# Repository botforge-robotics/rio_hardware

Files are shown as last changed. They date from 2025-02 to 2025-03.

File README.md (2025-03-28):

<p align="center">
    
    
    
    
    
    
    
    
    
</p>

<p align="center">
    <h1 align="center">RIO Hardware</h1>
</p>
<p align="center">
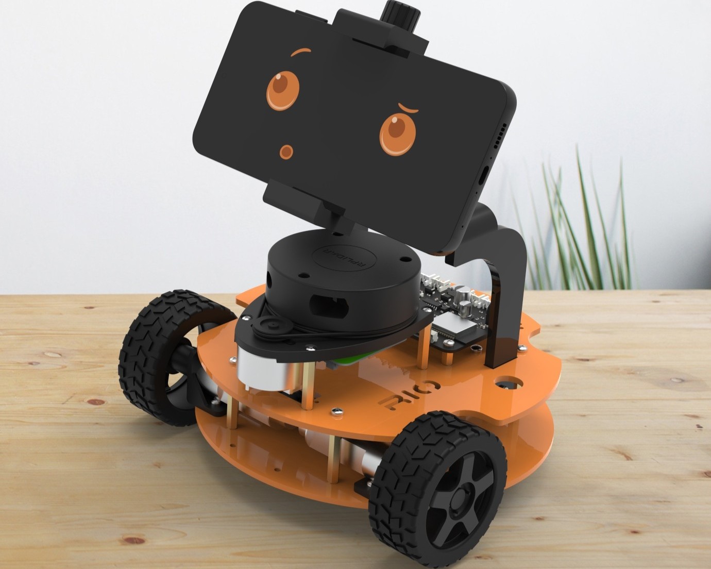
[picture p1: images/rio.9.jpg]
RIO Robot
    
</p>

## Table of Contents
- [Bill of Materials](#bill-of-materials)
  - [Hardware Components](#hardware-components)
  - [Software](#software)
    - [💰 Total Cost: ~₹14,269/-](#-total-cost-14269-)
  - [Fabrication Options](#fabrication-options)
    - [Option 1: Full 3D Printing](#option-1-full-3d-printing)
    - [Option 2: Hybrid (Recommended)](#option-2-hybrid-recommended)
  - [PCB Schematic](#pcb-schematic)
  - [Related Repositories](#related-repositories)
  - [🤝 Contributing](#-contributing)

## Description
This repository contains the Bill of Materials (BOM) for the RIO robot hardware parts and assembly. The RIO project aims to transform your smartphone into a fully-featured ROS2 robot, utilizing a wide array of built-in mobile sensors and custom hardware. The hardware design includes a custom PCB, motor drivers, and sensor integrations that work seamlessly with the RIO mobile app and ROS2 ecosystem.

# Bill of Materials

## Hardware Components
| No | Part Name | Description | Store | Quantity | Amount | Purchase Link |
|----|---|---|---|---|---|---|
| 1  | Dc-Motors with Encoders | TT Motor N20 12V 125RPM | Robu | 2 | ₹940 | [Link](https://robu.in/product/n20-12v-125rpm-metal-gear-motor-with-encoder-d-type-shaft/) |
| 2  | Wheels | 65mm Rubber Tyre Wheels | Robu | 2 | ₹330 | [Link](https://robu.in/product/65mm-robot-smart-car-12-rim-wheel-silver/) |
| 3  | Wheel Couplers | Short Coupling for Robot Smart Car Wheel | Robu | 2 | ₹160 | [Link](https://robu.in/product/short-coupling-for-robot-smart-car-wheel-4-mm-length-18mm/) |
| 4  | Caster Wheels | 30mm Dia and 37mm Height | Robu | 1 | ₹50 | [Link](https://robu.in/product/smart-car-wheel-trace-robot-patrol-line-vehicle) |
| 5  | Battery | 7.4V 2500mAh 3C Li-ion | Robu | 1 | ₹520 | [Link](https://robu.in/product/orange-18650-li-ion-2500mah-7-4v-2s1p-protected-battery-pack-3c) |
| 6  | Charger | 8.4V 1A Charger | Robu | 1 | ₹580 | [Link](#https://robu.in/product/lithium-battery-charger-8-4v-1a-with-dc-plug-2-indicators) |
| 7  | Lidar RP A1m8 | SLAMTECH RPLIDAR A1m8 | Robu | 1 | ₹8500 | [Link](https://robu.in/product/rp-lidar-a1m8-360-degrees-laser-range-finder) |
| 8  | Voltage Meter | 2S 18650 Li-Po Lithium Battery Capacity Indicator Module | Robu | 1 | ₹95 | [Link](https://robu.in/product/2s-18650-li-po-lithium-battery-capacity-indicator-module) |
| 9  | DC Jack For Voltage Meter | DC Jack Connector Male 2.1mm x 5.5mm with Wire | Robu | 1 | ₹45 | [Link](https://robu.in/product/dc-jack-connector-male-2-1mm-x-5-5mm-with-wire) |
| 10 | RGB LED | WS2812B LED Breakout Board | Robu | 2 | ₹30 | [Link](https://robu.in/product/cjmcu-123-ws2811-rgb-led-breakout-module) |
| 11 | Standoff MF Plastic M3 | 30mm Length | Robu | 4 | ₹35 | [Link](https://robu.in/product/m330mm-male-to-female-nylon-hex-spacer-10pcs) |
| 12 | Standoff MF Plastic M3 | 15mm Length | Robu | 4 | ₹24 | [Link](https://robu.in/product/m315mm-male-to-female-nylon-hex-spacer-10pcs) |
| 13 | Standoff MF Plastic M3 | 10mm Length | Robu | 4 | ₹25 | [Link](https://robu.in/product/m310mm-male-to-female-nylon-hex-spacer-10pcs-copy) |
| 14 | M3 Bolt Phillips | 6mm Length | Omrook | 8 | ₹5| [Link](https://omrook.com/fasteners/machine-screw/phillips-screw-with-washer/m3x6mm-phillip-with-washer-dia-3mm-length-6mm-machine-screw/) |
| 15 | M3 Bolt Phillips | 10mm Length | Omrook | 20 | ₹15 | [Link](https://omrook.com/fasteners/machine-screw/phillips-screw-with-washer/m3x10mm-phillip-with-washer-dia-3mm-length-10mm-machine-screw/) |
| 16 | M2.5 Bolt Phillips | 12mm Length | Omrook | 8 | ₹5 | [Link](https://omrook.com/fasteners/machine-screw/combi-head-screw/combi-screw-m2-5-x-12mm-screw-diameter-2-5mm-length-12mm/) |
| 17 | M3 Nuts | Nylock | Omrook | 20 | ₹25 | [Link](https://omrook.com/fasteners/nut/nyloc-nut/3mm-nyloc-nut-m3/) |
| 18 | Mobile Mount | Mobile Holder with Adjustable Clamp | Amazon | 1 | ₹195 | [Link](https://www.amazon.in/gp/product/B08W1KX225/ref=ppx_yo_dt_b_asin_title_o02_s01?ie=UTF8&th=1) |
| 19 | Mobile Ball Joint | Universal 1/4" Screw Swivel Ball Head Tripod Mount | Amazon | 1 | ₹200 | [Link](https://www.amazon.in/gp/product/B0BCFPNFCF/ref=ppx_yo_dt_b_asin_title_o02_s00?ie=UTF8&th=1) |
| 20 | Chassis | Laser Cutting/3D Printed Parts | self | - | ₹400 | [Build Your Own](#fabrication-options)  |
| 21 | PCB | Custom PCB | self | 1 | ₹1000 | [Build Your Own](#pcb-schematic) |

## Software
| Component | Description | Store | License | Cost | Link |
|---|---|---|---|---| ---|
| **RIO Mobile App** | Android application for robot control and sensor integration | Play Store | Single User | ₹990  |  [Link](https://play.google.com/store/apps/details?id=com.botforge.rio) |

> Note: The RIO Mobile App is not a required component for operating the robot, but it enables the use of smartphone sensors and transforms your robot into a companion robot with advanced features.

<div align="center">

### 💰 Total Cost: ~₹14,269/-

</div>

---

## Fabrication Options

The RIO robot chassis can be fabricated using either full 3D printing or a hybrid approach combining laser cutting and 3D printing. Here are the details for both options:

### Option 1: Full 3D Printing
All parts are available as STL files in the `3dPrinting` folder:

**Base Components:**
- [`base_bottom.stl`](./3dPrinting/base_bottom.stl) - Bottom plate of the chassis.
- [`base_top.stl`](./3dPrinting/base_top.stl) - Top plate of chasis.
- [`motor_bracket_left.stl`](./3dPrinting/motor_bracket_left.stl) & [`motor_bracket_right.stl`](./3dPrinting/motor_bracket_right.stl) - Motor mounting brackets.

**Mobile Phone Mount:**
- [`mobile_holder_base_top.stl`](./3dPrinting/mobile_holder_base_top.stl) - Top connecting piece
- [`mobile_holder_base_side_left.stl`](./3dPrinting/mobile_holder_base_side_left.stl) & [`mobile_holder_base_side_right.stl`](./3dPrinting/mobile_holder_base_side_right.stl) - Mount side connecting side pieces
- [`mobile_holder_top_bracket_left.stl`](./3dPrinting/mobile_holder_top_bracket_left.stl) & [`mobile_holder_top_bracket_right.stl`](./3dPrinting/mobile_holder_top_bracket_right.stl) - Top connecting brackets
- [`mobile_holder_bracket_left.stl`](./3dPrinting/mobile_holder_bracket_left.stl) & [`mobile_holder_bracket_right.stl`](./3dPrinting/mobile_holder_bracket_right.stl) - Mounting brackets holder to chasis

**LED Holders:**
- [`ws2812b_holder_left.stl`](./3dPrinting/ws2812b_holder_left.stl) & [`ws2812b_holder_right.stl`](./3dPrinting/ws2812b_holder_right.stl) - RGB LED mounting brackets

<p align="center">
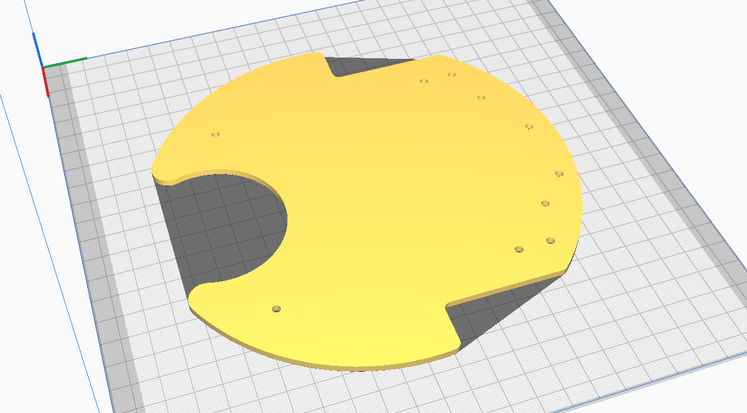
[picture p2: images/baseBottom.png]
Base Bottom
    
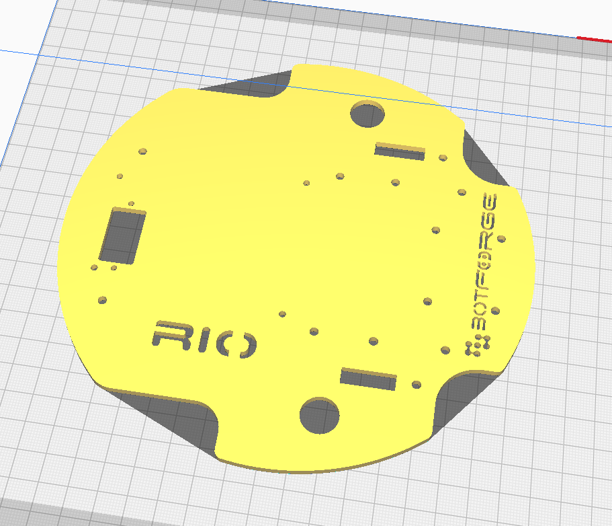
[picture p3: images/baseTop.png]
Base Top
    
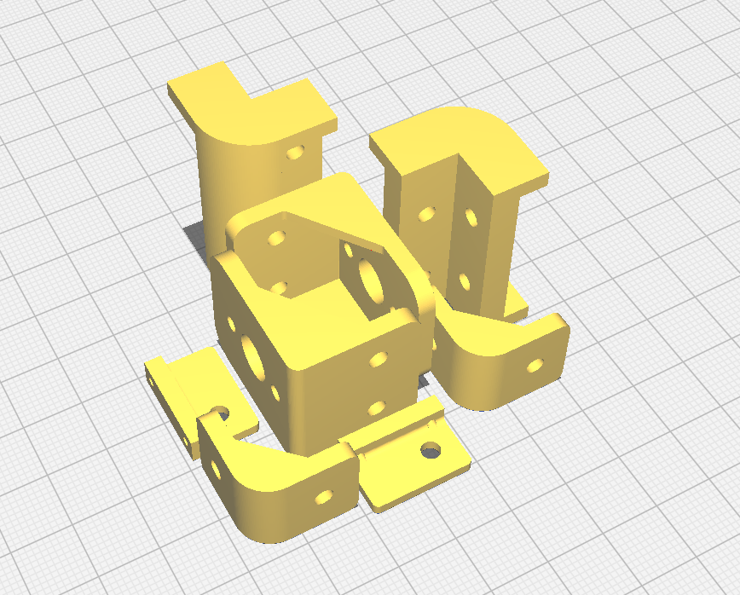
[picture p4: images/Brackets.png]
3D Printed Brackets
    
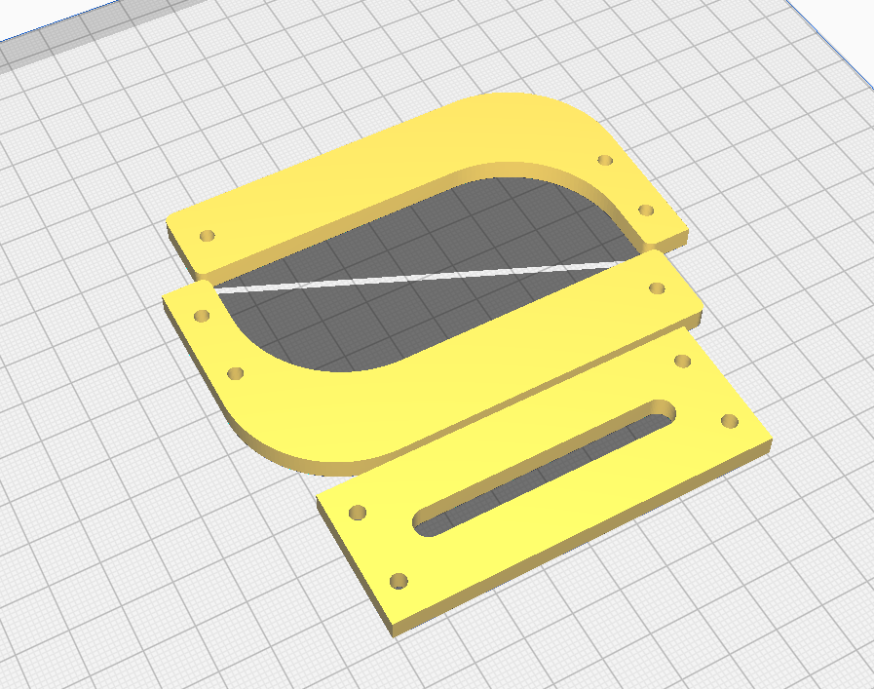
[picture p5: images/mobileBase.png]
Mobile Base
    
</p>

### Option 2: Hybrid (Recommended)
For better durability and professional finish, you can use a combination of laser cutting and 3D printing:

**Laser Cut Parts & Files:**
- Base Components (3mm Acrylic):
  - [`base_bottom_3mm.dxf`](./laserCuting/base_bottom_3mm.dxf) - Bottom plate of the chassis
  - [`base_top_3mm.dxf`](./laserCuting/base_top_3mm.dxf) - Top plate of the chassis

- Mobile Phone Mount (5mm Acrylic):
  - [`mobile_base_top_5mm.dxf`](./laserCuting/mobile_base_top_5mm.dxf) - Top piece
  - [`mobile_base_side_left_5mm.dxf`](./laserCuting/mobile_base_side_left_5mm.dxf) - Left side piece
  - [`mobile_base_side_right_5mm.dxf`](./laserCuting/mobile_base_side_right_5mm.dxf) - Right side piece

- Complete Design File:
  - [`all_files_laser_cutting.cdr`](./laserCuting/all_files_laser_cutting.cdr) - CorelDRAW-v11 format with all components

<p align="center">
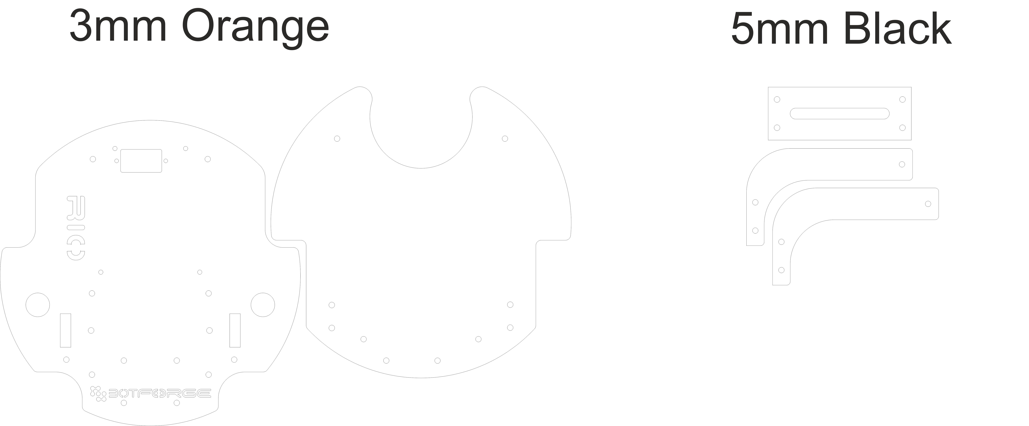
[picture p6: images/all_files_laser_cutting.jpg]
Laser Cut Parts
    
</p>

**3D Printed Parts:**
- Motor Mounts:
  - [`motor_bracket_left.stl`](./3dPrinting/motor_bracket_left.stl) - Left motor bracket
  - [`motor_bracket_right.stl`](./3dPrinting/motor_bracket_right.stl) - Right motor bracket

- Mobile Phone Mount Brackets:
  - [`mobile_holder_bracket_left.stl`](./3dPrinting/mobile_holder_bracket_left.stl) - Left mounting bracket
  - [`mobile_holder_bracket_right.stl`](./3dPrinting/mobile_holder_bracket_right.stl) - Right mounting bracket
  - [`mobile_holder_top_bracket_left.stl`](./3dPrinting/mobile_holder_top_bracket_left.stl) - Left top bracket
  - [`mobile_holder_top_bracket_right.stl`](./3dPrinting/mobile_holder_top_bracket_right.stl) - Right top bracket

- LED Holders:
  - [`ws2812b_holder_left.stl`](./3dPrinting/ws2812b_holder_left.stl) & [`ws2812b_holder_right.stl`](./3dPrinting/ws2812b_holder_right.stl) - RGB LED mounting brackets

> Note: The hybrid approach (Option 2) is recommended for better durability and professional appearance. However, full 3D printing is perfectly viable for prototyping or if laser cutting is not available.

## PCB Schematic
<p align="center">
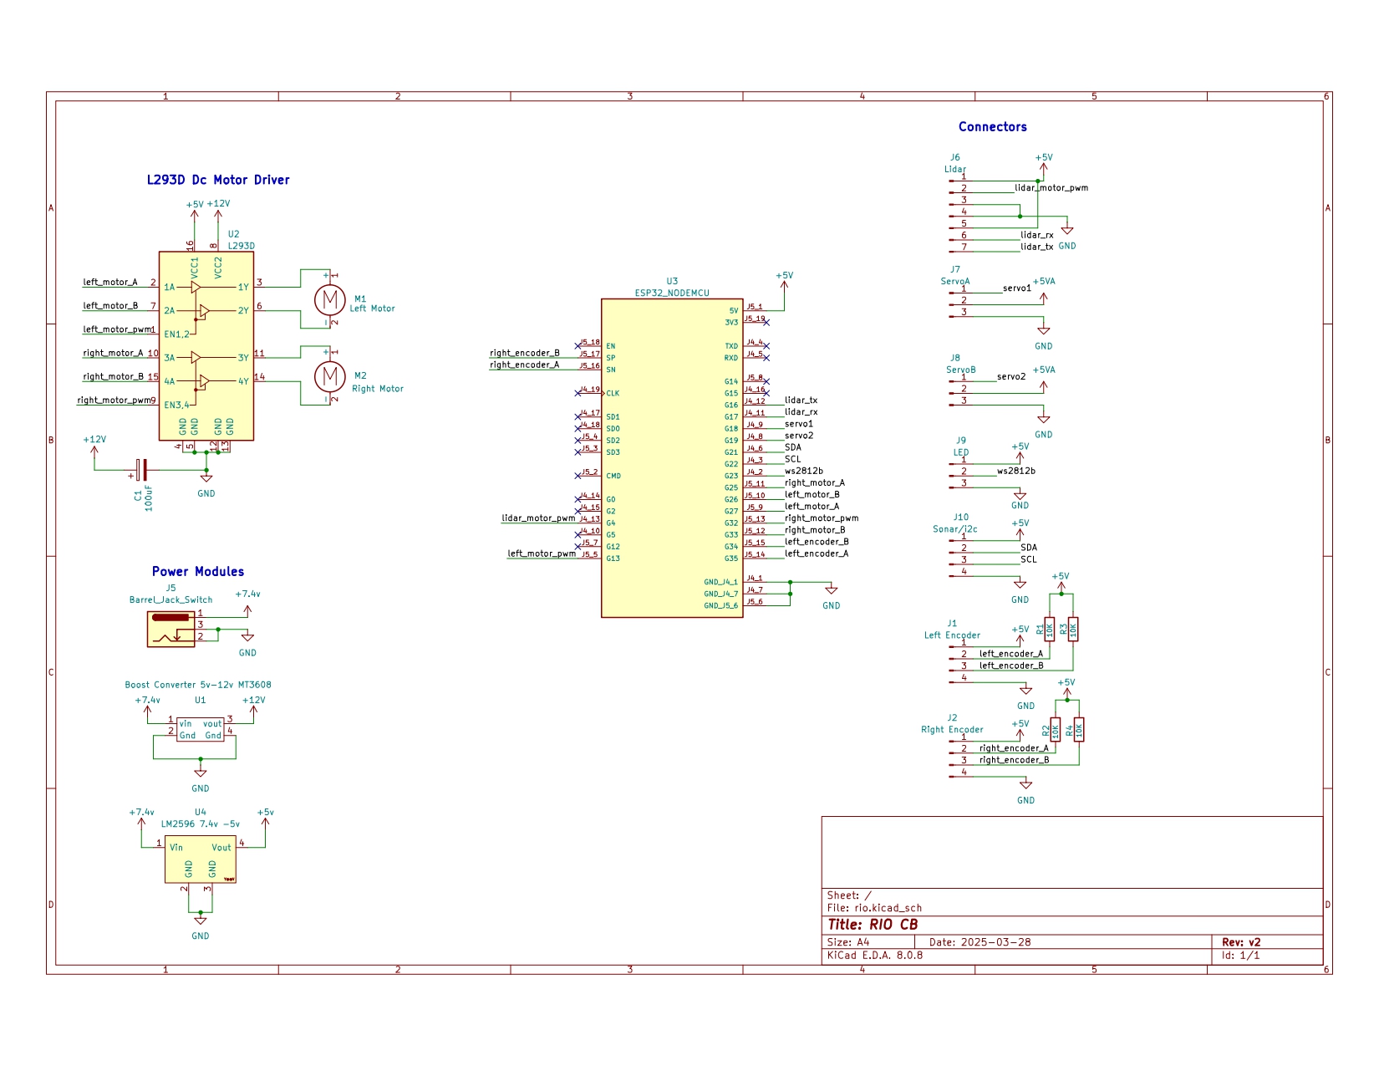
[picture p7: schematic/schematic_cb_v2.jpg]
PCB Schematic
    
</p>

You can download the full schematic as a PDF: [Download Schematic PDF](./schematic/schematic_cb_v2.pdf)

## Related Repositories
- 🔧 [RIO Firmware](https://github.com/botforge-robotics/rio_firmware) - RIO Controller Micro-Ros Code
- 🤖 [RIO ROS2](https://github.com/botforge-robotics/rio_ros2) - ROS2 packages for navigation, control, and sensor integration

## 🤝 Contributing
1. Fork the Repository
2. Create Feature Branch
3. Commit Changes
4. Push to Branch
5. Open Pull Request

---

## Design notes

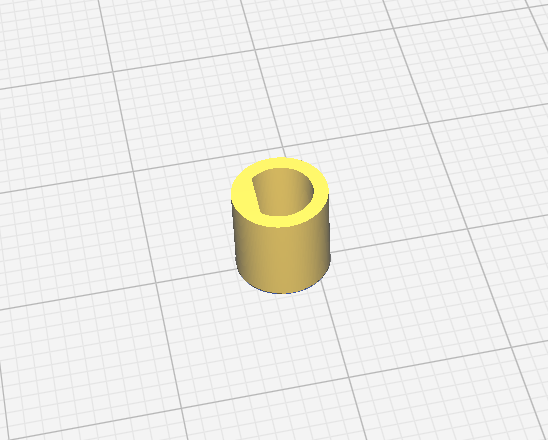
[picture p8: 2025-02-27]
images/wheelBush.png

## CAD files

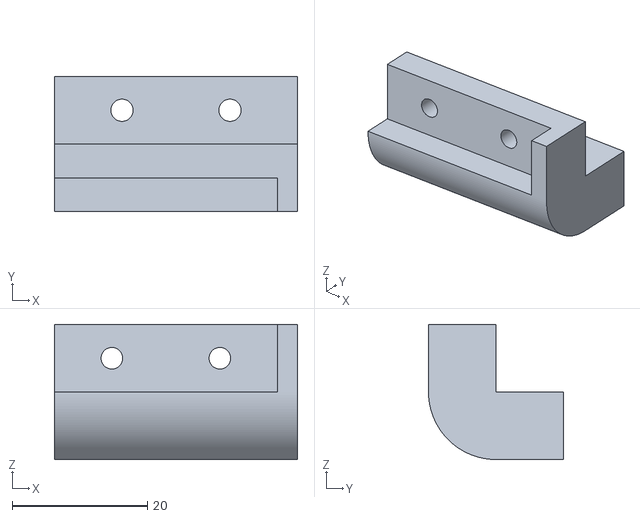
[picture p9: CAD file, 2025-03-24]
3dPrinting/mobile_holder_top_bracket_left.stl
36.0 x 20.0 x 20.0

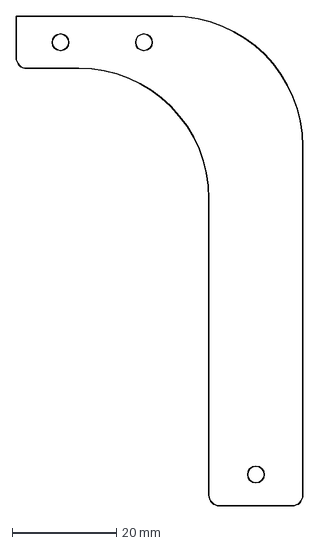
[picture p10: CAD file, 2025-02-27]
laserCuting/mobile_base_side_left_5mm.dxf
55.0 x 94.0 mm

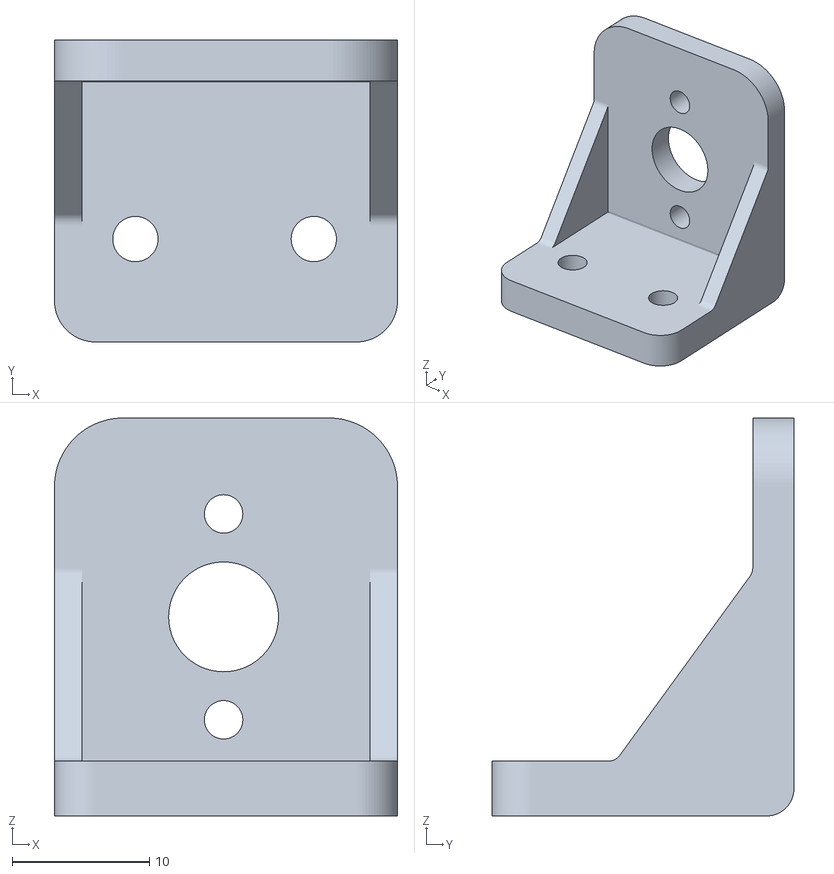
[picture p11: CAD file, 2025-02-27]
3dPrinting/motor_bracket_left.stl
25.0 x 22.0 x 29.0

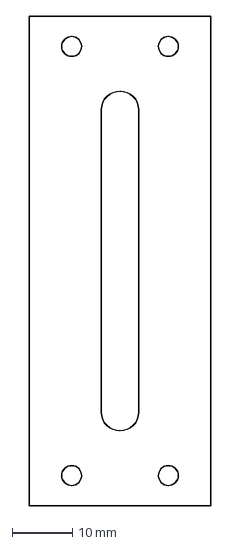
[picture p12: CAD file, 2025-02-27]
laserCuting/mobile_base_top_5mm.dxf
30.0 x 81.0 mm

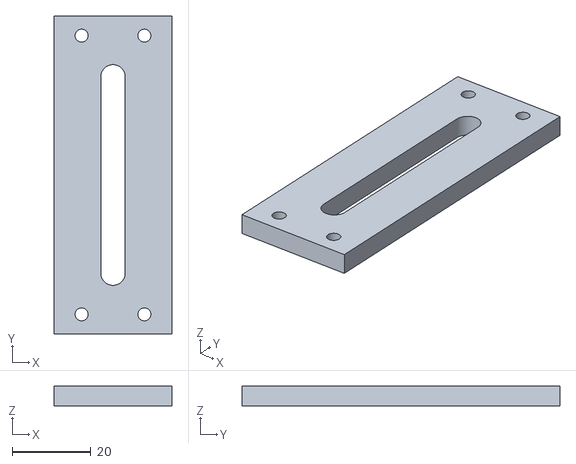
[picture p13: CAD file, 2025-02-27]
3dPrinting/mobile_holder_base_top.stl
30.0 x 81.0 x 5.00

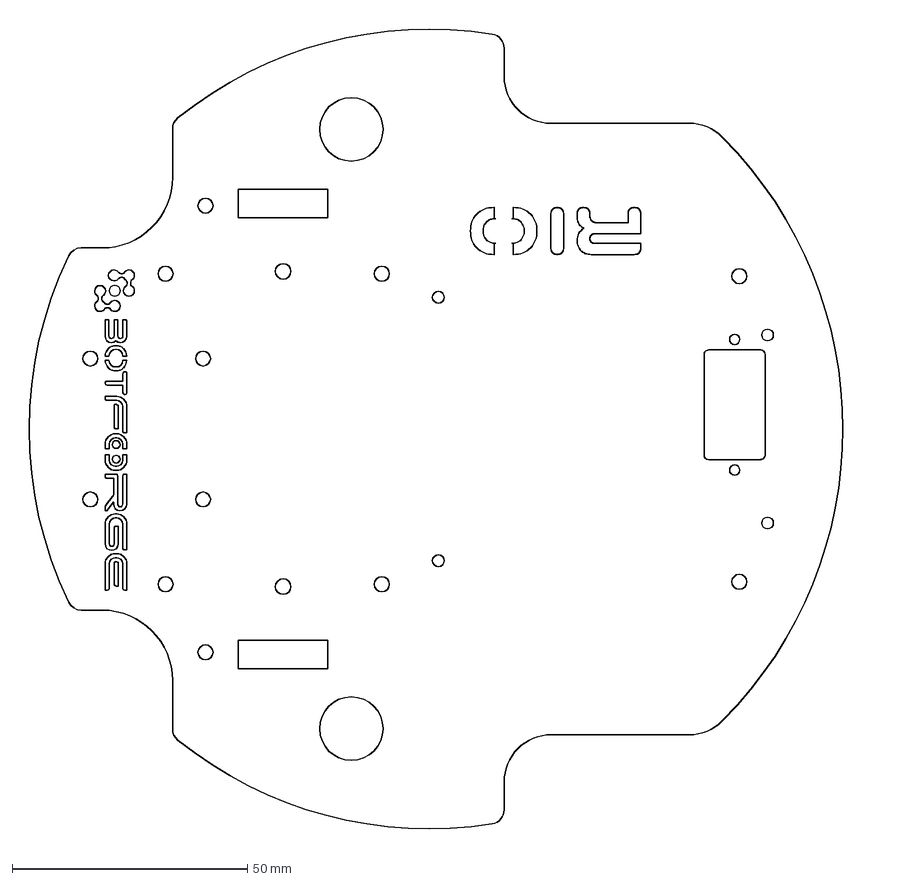
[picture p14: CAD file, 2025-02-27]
laserCuting/base_top_3mm.dxf
184.3 x 175.5 mm

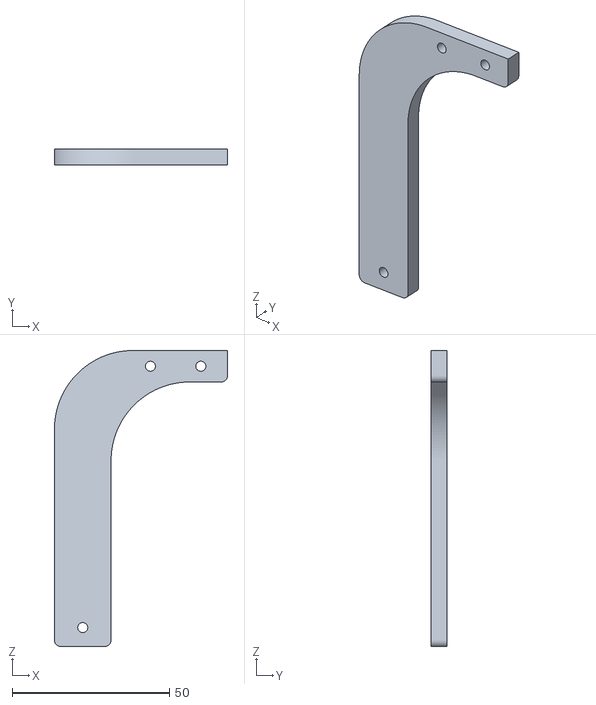
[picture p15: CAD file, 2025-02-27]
3dPrinting/mobile_holder_base_side_right.stl
55.0 x 5.00 x 94.0

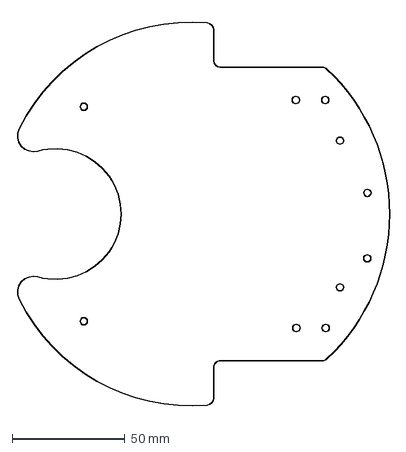
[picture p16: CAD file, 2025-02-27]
laserCuting/base_bottom_3mm.dxf
165.4 x 175.3 mm

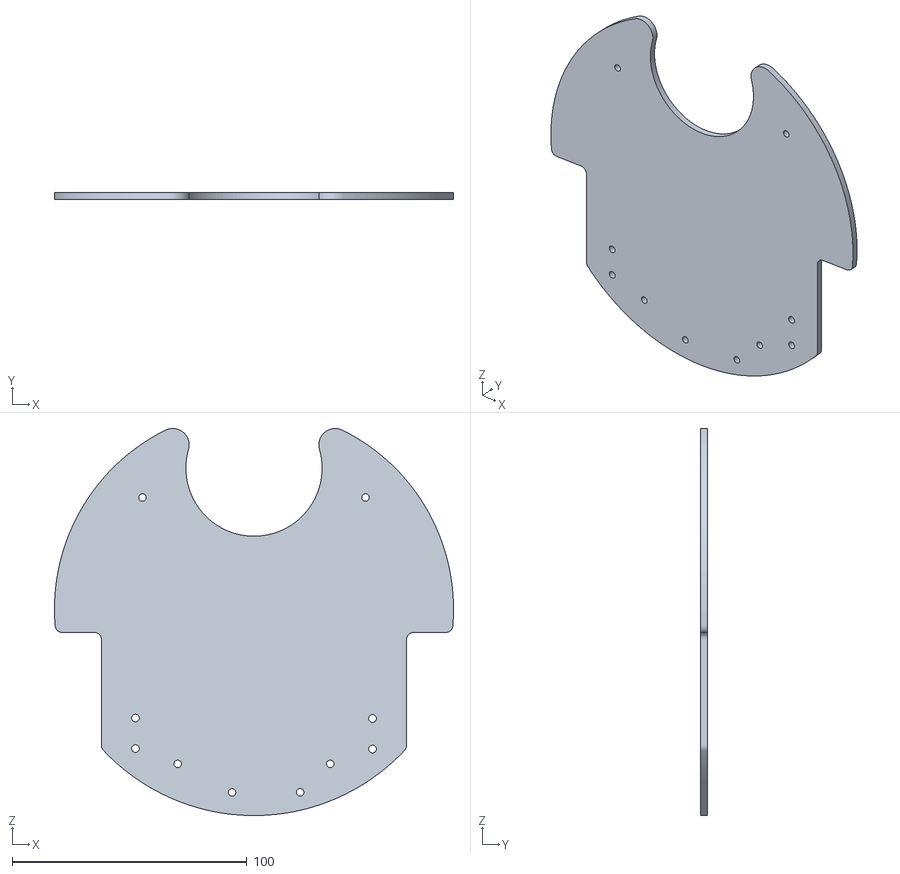
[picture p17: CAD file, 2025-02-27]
3dPrinting/base_bottom.stl
170.0 x 3.00 x 164.9

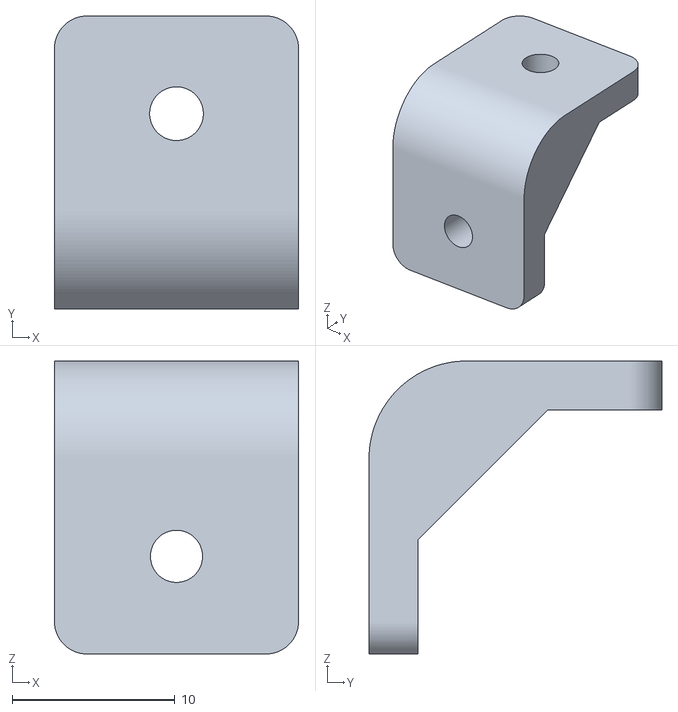
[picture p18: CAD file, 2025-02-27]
3dPrinting/mobile_holder_bracket_left.stl
15.0 x 18.0 x 18.0

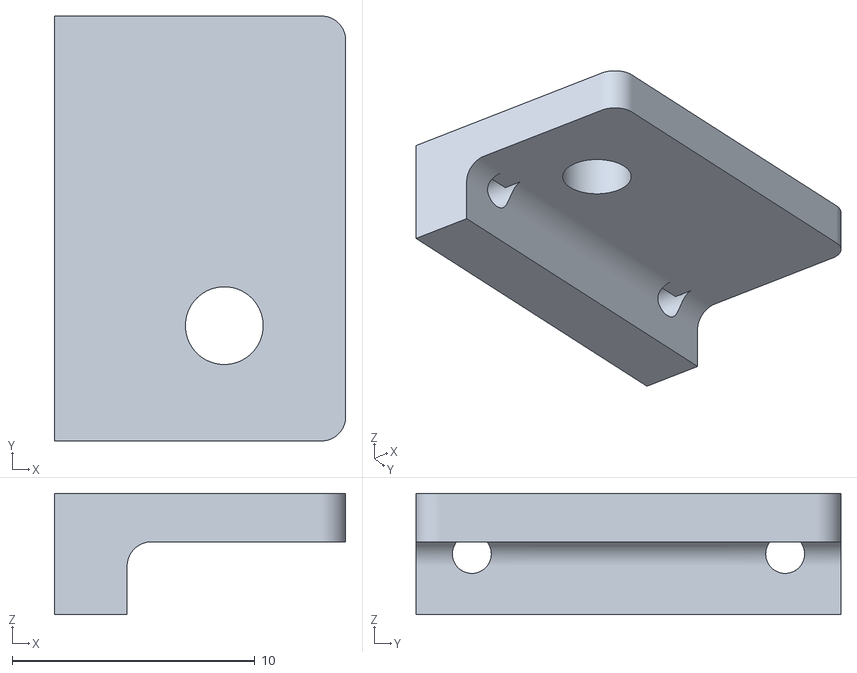
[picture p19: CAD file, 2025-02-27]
3dPrinting/ws2812b_holder_left.stl
12.0 x 17.5 x 5.00

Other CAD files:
3dPrinting/mobile_holder_top_bracket_right.stl
3dPrinting/mobile_holder_base_side_left.stl
3dPrinting/ws2812b_holder_right.stl

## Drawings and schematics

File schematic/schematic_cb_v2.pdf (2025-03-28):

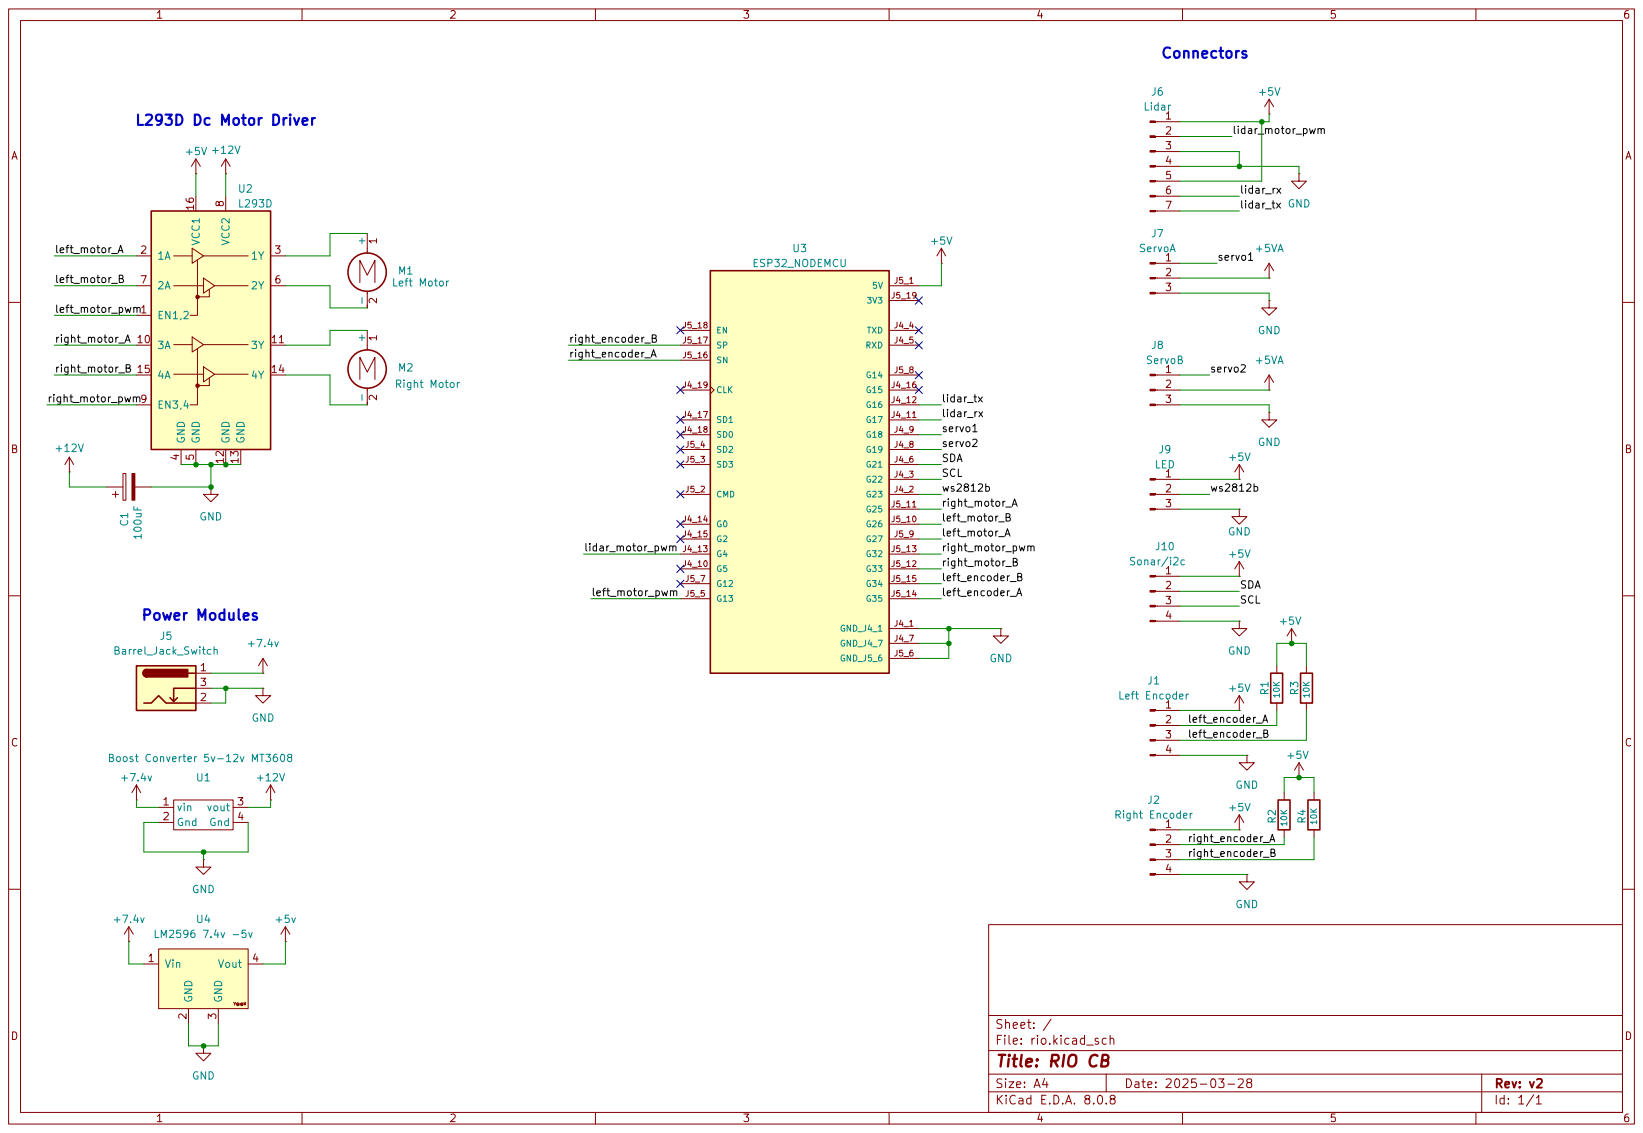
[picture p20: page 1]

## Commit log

2025-02-27 intial release added machineing files and bom
    [BOM.csv, base_bottom.stl, base_bottom_3mm.dxf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]
2025-03-02 Remove BOM.csv and wheelBush.stl, update README with comprehensive documentation
    [BOM.csv, wheelBush.stl]
2025-03-02 Update BOM with revised chassis cost and total project cost
2025-03-28 added schematic

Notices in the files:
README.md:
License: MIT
